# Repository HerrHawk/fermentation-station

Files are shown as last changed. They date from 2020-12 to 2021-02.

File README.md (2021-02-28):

# Fermenation Station

# About the Project

The motivation behind *Fermentation Station* was to have an easy way of maintaining a controlled environment (meaning temperature and humidity). Fermentation is a fickle process and maintaining the desired temperature and humidity in a stable manner is crucial for providing a safe and delicious product. Thus the premise is simple: have a contained system which handles everything you need to worry about. Set a target temperature and humidity value, put your produce in the box and come back in a couple of days to your ferment.

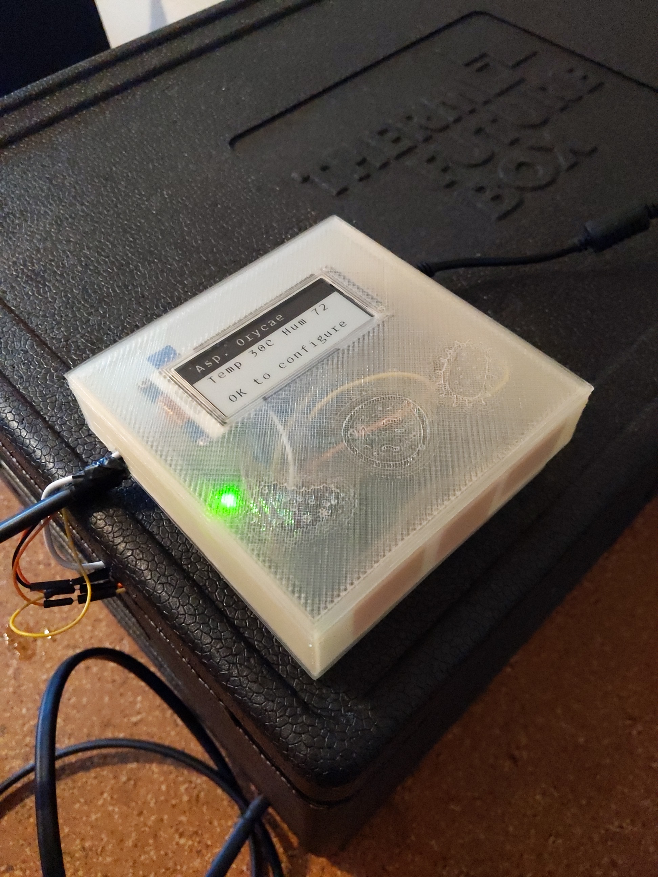
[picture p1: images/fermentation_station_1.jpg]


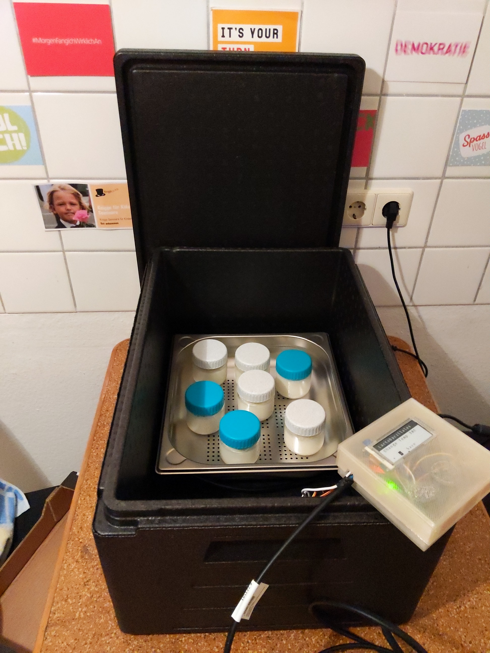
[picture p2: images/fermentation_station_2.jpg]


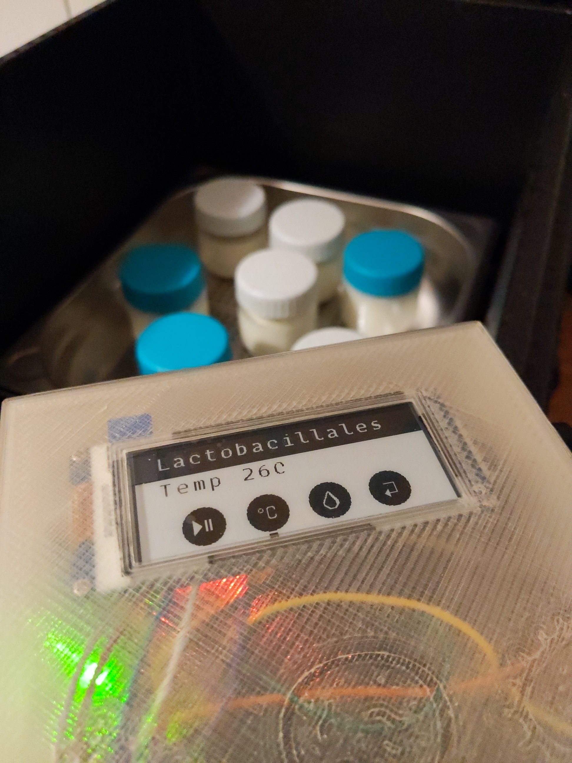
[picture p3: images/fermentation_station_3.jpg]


# How to use it

The user has three capacitive buttons to press: a `-`, `+` and `ok` button.

1. Connect the Fermentation Station to a power socket and wait for it to boot
2. On the recipe selection screen, use the `-` and `+` buttons to select a recipe
3. Confirm your selection with the `ok` button
4. If you need to, change the temperature and humidity to your desired values
5. Start the fermentation process
6. Come back in a couple of days and enjoy your ferment!

# Setup

## Hardware

|Product |Notes |Order |Datasheet |
|---|---|---|---|
|Adafruit Trinket Pro 3V |Main controller. Runs on 3.3V & comes with an onboard USB bootloader. |[Link](https://www.adafruit.com/product/2010) |[Link](https://cdn-shop.adafruit.com/datasheets/ATMEGA328P.pdf) |
|Arduino Uno |Used as a FTDI adapter for flashing and debugging the TrinketPro. |[Link](https://store.arduino.cc/arduino-uno-rev3) |[Link](http://ww1.microchip.com/downloads/en/DeviceDoc/Atmel-7810-Automotive-Microcontrollers-ATmega328P_Datasheet.pdf)|
|Bosch BME280 |Humidity/Temperature/Pressure Sensor (Pressure functionality is not used in this project). |[Link](https://www.reichelt.de/de/de/entwicklerboards-temperatur-feuchtigkeits-und-drucksensor--debo-bme280-p253982.html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) |[Link](https://www.mouser.de/datasheet/2/783/BST_BME280_DS002-1509607.pdf) |
|DEBO TOUCH SENS2 MPR121 |Capacitive touch controller with up to 12 Input channels (Three are used in this project). |[Link](https://www.reichelt.de/entwicklerboards-platine-fuer-kapazitive-beruehrungssensoren-mp-debo-touch-sens2-p291455.html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) |[Link](https://cdn-reichelt.de/documents/datenblatt/A300/DEBO_TOUCH_SENS2_DS_EN.pdf) |
|Waveshare 2.9inch e-Paper Module|E-Ink display for rendering information about the fermentation process. |[Link](https://www.reichelt.de/entwicklerboards-display-epaper-2-9-schwarz-weiss-debo-epa-2-9-p224224.html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) |[Link](https://www.waveshare.com/w/upload/9/98/2.9inch-e-paper-module-user-manual-en.pdf) |
|Ultrasonic Nebulizer |Compact humidifier, USB powered piezoelectric transducer that generates fine mist. |[Link](https://www.amazon.de/PEARL-Nebler-USB-Mini-Luftbefeuchter-Aroma-Diffuser/dp/B08591SF5G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) (Double Pack)|- |
|MOSFET Module DC 5V-36V 15A |Used to regulate the output of the heating element & humidifier. |[Link](https://www.amazon.de/gp/product/B07VRCXGFY/ref=ppx_yo_dt_b_asin_title_o03_s00?ie=UTF8&psc=1) (5 pcs) |- |
|DC/DC Step Down Buck Converter  |Converts the 24V from the Power Supply to 5V to drive the Arduino. A screwdriver and multimeter is required to set the correct output voltage.|[Link](https://www.amazon.de/gp/product/B08DNVXP87/ref=ppx_yo_dt_b_asin_title_o05_s00?ie=UTF8&psc=1) (6 pcs) |- |
|Thermo Box 42L |We used a 42 Liter Thermo Box for our prototype. In combination with the 30W Heatingcable we don't recommend going with a bigger box. |[Link](https://www.amazon.de/gp/product/B07B924LBB/ref=ppx_yo_dt_b_asin_title_o09_s00?ie=UTF8&psc=1) |- |
|Heating Cable 30W |24V 30W Heating cable with IPx7 protection. Ideal for our use-case. |[Link](https://www.amazon.de/gp/product/B00BAQW0OM/ref=ppx_yo_dt_b_asin_title_o01_s00?ie=UTF8&psc=1) |- |
|Power Supply 24 V 6A AC/DC | |[Link](https://www.amazon.de/gp/product/B0721MKCZJ/ref=ppx_yo_dt_b_asin_title_o03_s00?ie=UTF8&psc=1) |- |

Overall, the listed items set us back with around 140€. Costs could be reduced if we ordered from Chinese manufacturers via AliExpress, but this would result in much longer delivery times.

We choose all our components, if available, as breakout boards for an easy time while developing and prototyping. Since they aren't hardwired into the final prototype, they can easily be removed and reused for other projects.

Additionally, we used some miscellaneous hardware like breadboards, (jumper) wires and copper plates.

A soldering iron is also required for preparing the modules and building the prototype.

### Connecting the hardware

The schematic for this project is not too complicated. Since we choose manly hardware that is available as breakout boards and communicate via protocols like I²C and SPI, the wiring is kept at a minimum. While most of the build is only connecting pins, the chosen parts do need some preparation, before they can be used. Most of the components come with loose pin headers, which need to be soldered on to boards. After that, we are ready to go.  To get an idea of the whole build we created a breadboard and technical schematic in [fritzing](https://fritzing.org/). Some parts in the schematic defer from the ones in our part list, since they weren't available in fritzing, but the wiring stays the same. 

**Breadboard:**

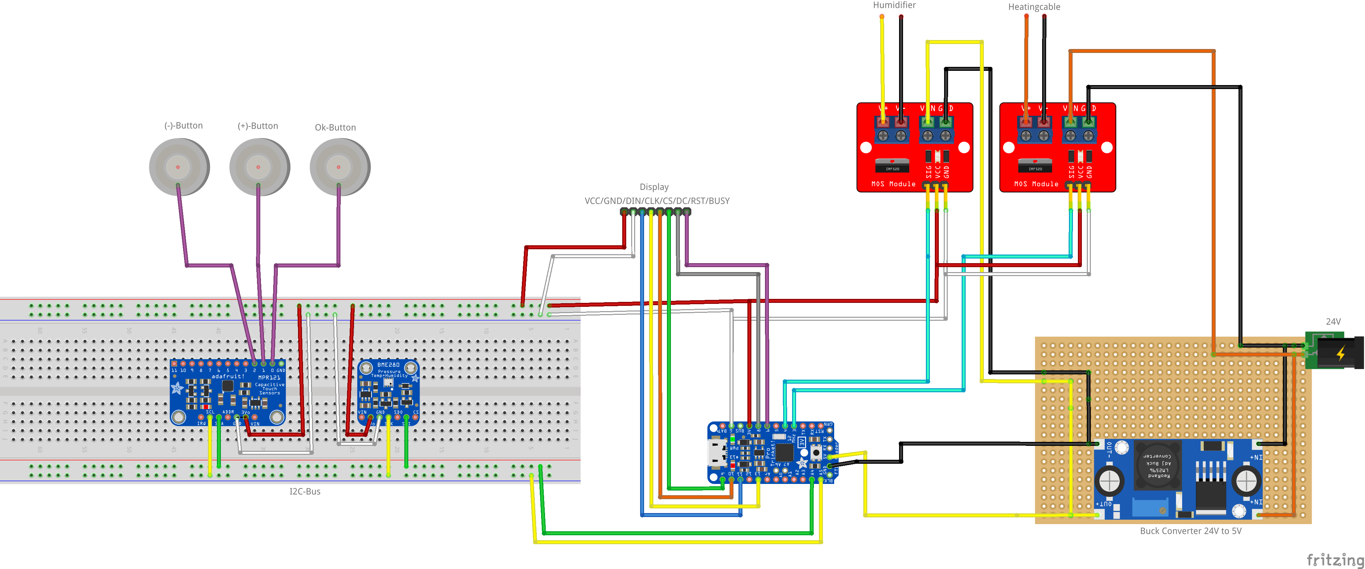
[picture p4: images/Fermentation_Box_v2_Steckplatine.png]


**Circuit diagram:**

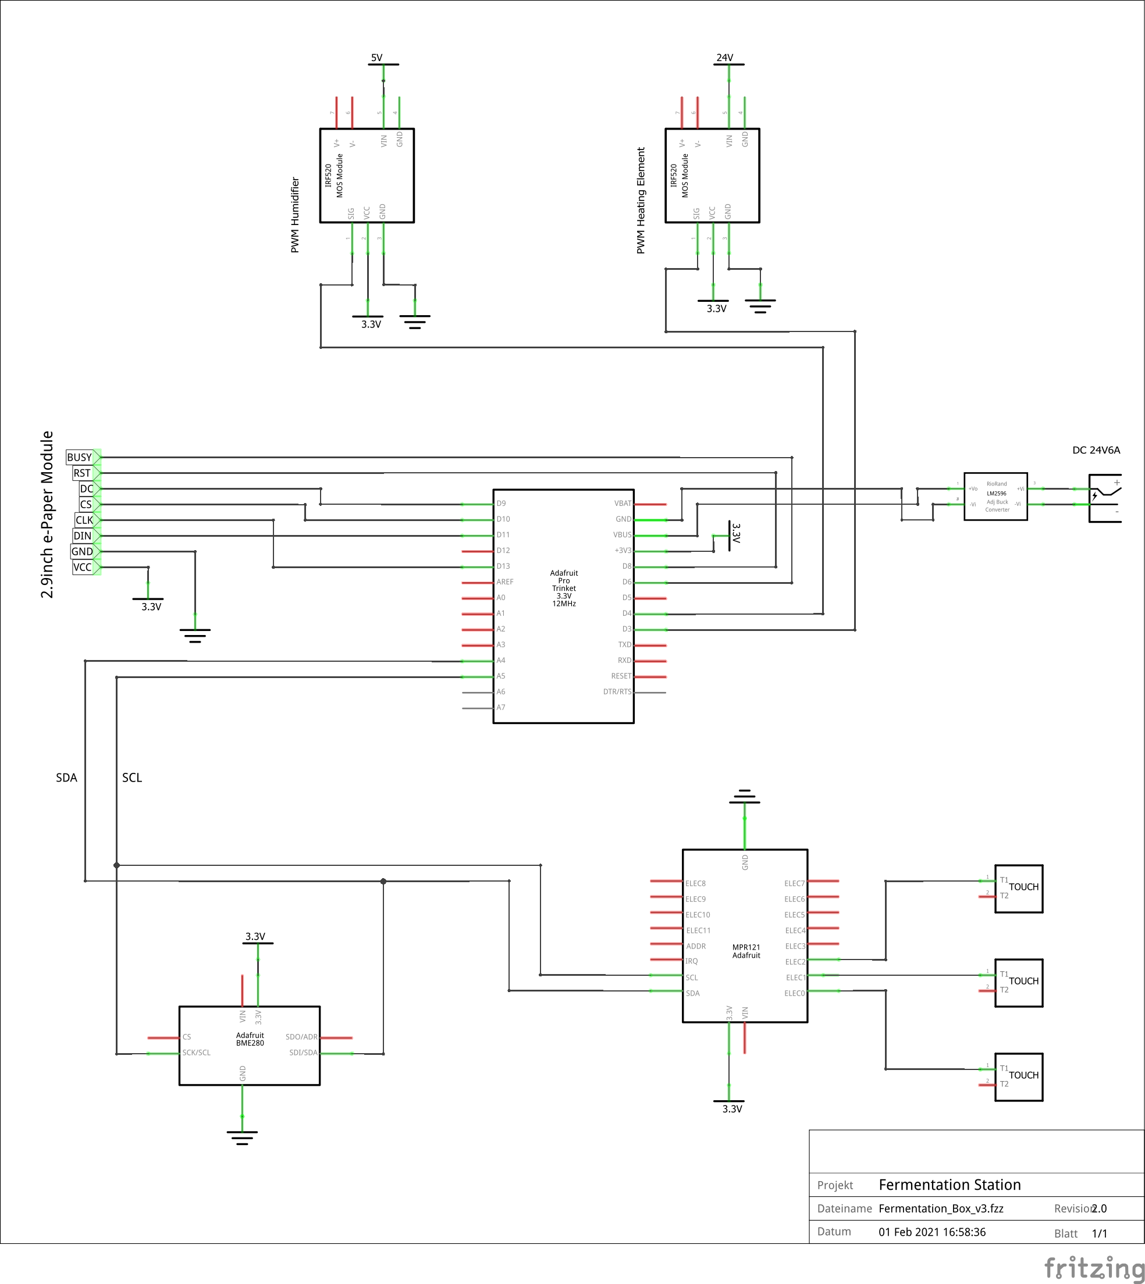
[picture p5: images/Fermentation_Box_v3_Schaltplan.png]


### Testing the individual components

Before putting everything together we recommend testing the individual parts separately. During our build we encountered problems especially with the e-Ink display. Checking the bought hardware early will prevent unnecessary delays later on. 

The chosen components come all with example code from the manufacturers or distributors like Adafruit. All the examples can be built and run with the Arduino IDE.

- **Waveshare e-Ink Display: [GitHub](https://github.com/waveshare/e-Paper)**
    - Run the demo code in */Arduino/epd2in9/epd2in9.ino*
    - If the TrinketPro is used for testing, change the BUSY pin defined in /Arduino/epd2in9/epdif.h from 7 to 6. (Pin 7 on the TrinketPro isn't exposed and reserved for the onboard USB connection)
- **BME280: [Adafruit](https://learn.adafruit.com/adafruit-bme280-humidity-barometric-pressure-temperature-sensor-breakout/arduino-test)**
    - On the linked website you find a detailed explanation on how to add and run the example code in the Arduino IDE for the BME280-Sensor.
- **MPR121: [Adafruit](https://learn.adafruit.com/adafruit-mpr121-12-key-capacitive-touch-sensor-breakout-tutorial?view=all)**
    - Same goes for the touch sensor. Add the example code to the IDE and test the touch sensor.
    - After testing the touch sensor we recommend switching to bigger electrodes. This makes controlling and testing the fermentation station easier. We used simple [copper foil](https://www.conrad.de/de/p/pb-fastener-kupferfolie-selbstklebend-l-x-b-150-mm-x-30-mm-inhalt-10-st-529532.html) to build our electrodes.

After testing the individual components they can be combined according to our schematics.

After development, we tried to go for a more permanent setup. We replaced the breadboard with a perfboard. Instead of soldering our microcontroller and sensors directly onto the perfboard we used pin headers, so the modules can be easily attached or removed if we want to reuse them for other projects. Since it was our first attempt at soldering a permanent prototype the result isn't perfect, but it does the job.

To prevent damage to the hardware components and wiring we 3D-printed a simple case for our prototype. We added a cutout in the top of the box for the display. The electrodes were placed inside the box. The electrodes can reliably detect touch input through the plastic - No buttons needed!

<!-- ![images/fermentation_station_4.jpg](images/fermentation_station_4.jpg) -->
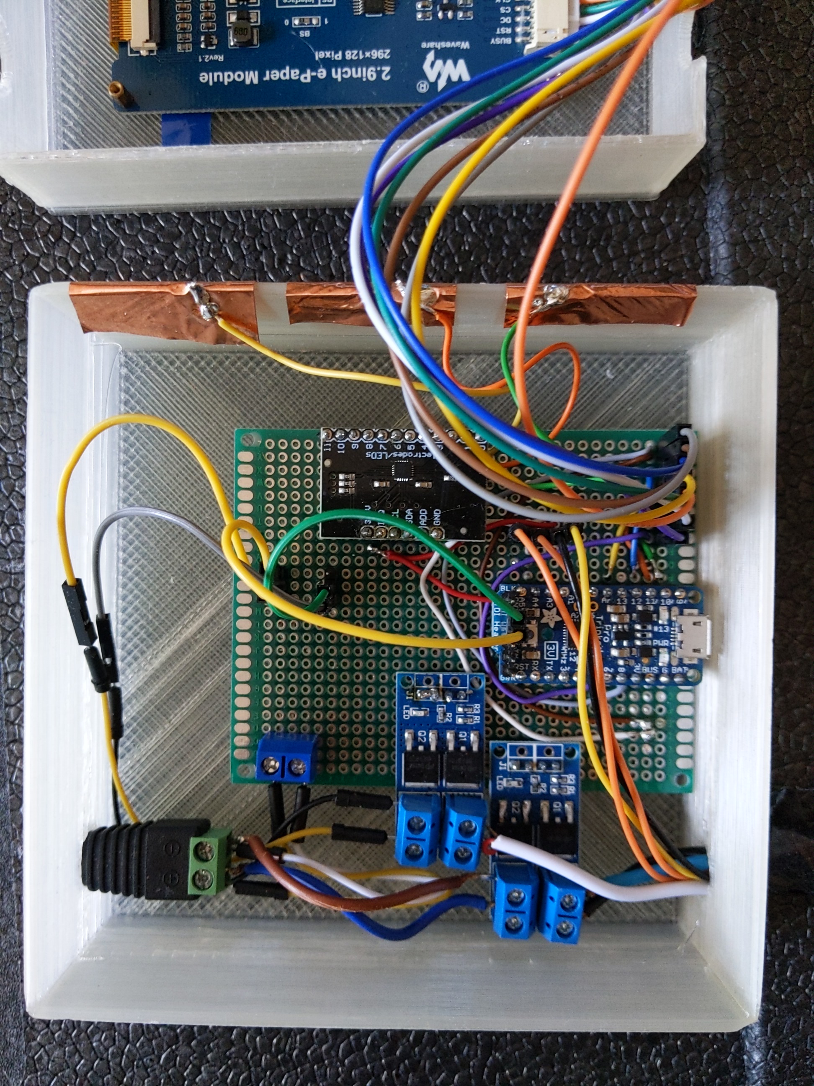
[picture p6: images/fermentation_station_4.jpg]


<!-- ![images/fermentation_station_5.jpg](images/fermentation_station_5.jpg) -->
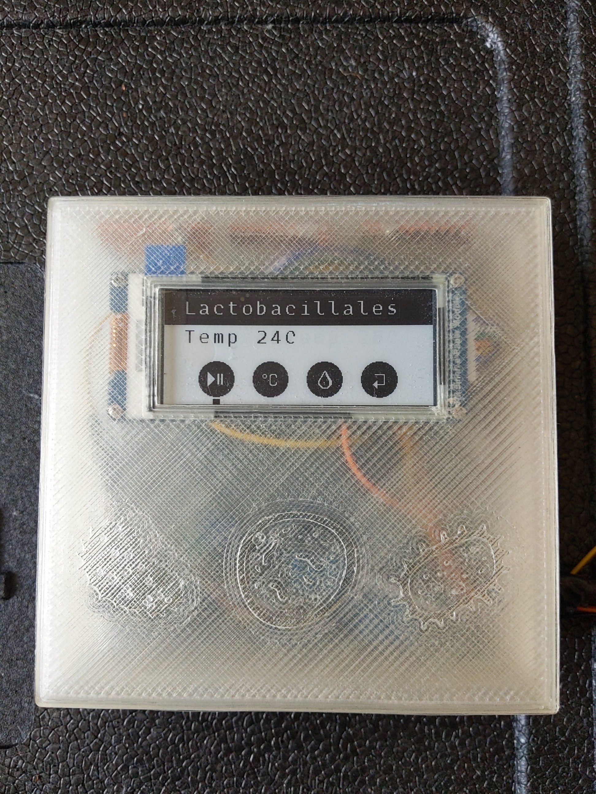
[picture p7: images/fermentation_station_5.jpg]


## Software

The project is written in embedded C, no external libraries are used. Additionally, for font rendering we use Python to create the individual character bitmaps.

### Building and Flashing

To be able to build and flash the firmware onto the microcontroller, you need to have [avr-gcc](https://www.google.com/search?client=safari&rls=en&q=avrgcc&ie=UTF-8&oe=UTF-8) and avrdude installed. On Windows, [WinAVR](http://winavr.sourceforge.net) can be used as an alternative to avr-gcc. 

The build process is handled via a Makefile. In order to get started with building, simply execute the following commands in the root folder of the repository.

```bash
> cd <repo-dir>
> mkdir build
> make clean
> make build
> make flash
```

`make clean` sets us up with a bland slate, deleting all files created in the build process. This also forces a complete rebuild.

`make build` bundles all the code into a format that can be flashed onto the microcontroller.

`make flash` flashes the previously build .hex file onto the microcontroller. This also executes `build` beforehand.

## Implementation Details

### Design Principles

- Rely on CI/CD for catching breaking changes early
- Clang format for enforced coding styles
- As functional as possible - no faked Classes in C!
- Work with git and feature branches

### Architecture

Our architecture consists of a hardware interface layer, a driver layer, a controller layer and the main program flow which is implemented as a state machine. We have split the code in modules beginning from the components that communicate directly with the hardware up to the high-level functions that we use to control the sensors & actors. This keeps the code well-arranged. 

- The Hardware Interfaces Layer represents the low-level protocols that we implemented. In our project SPI is used to communicate with the display, UART for writing to the display and I2C for retrieving sensor information from the temperature/humdity sensor and the touch sensor.
- The Drivers Layer contains an API that our controller layer can use to execute functions that work on the different hardware components.
- The Controller Layer provides high-level functions to interact with the different hardware and sensors. An example is the Renderer that can write text and images onto the display. Some example functions and more implementation details on the Renderer are shown in chapter Font and Image Rendering
- The state machine, which is explained in detail in the following chapter, is used to control the program flow. Additionally, it writes errors that occur to the Serial Port (using our Logging controller).

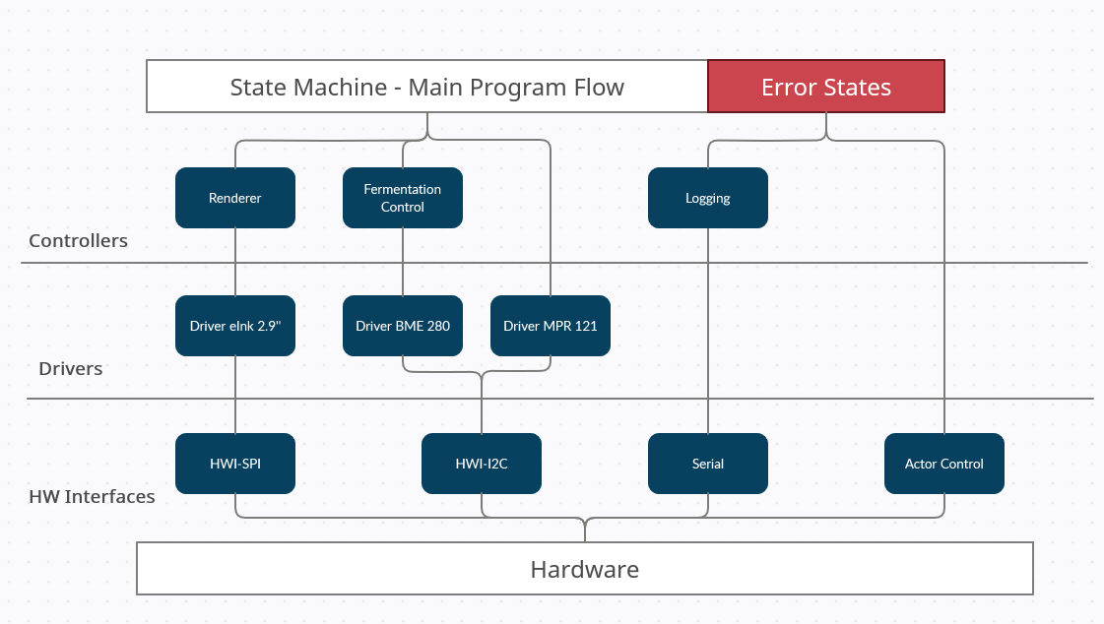
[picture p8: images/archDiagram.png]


### State Machine

For controlling the main program flow we used a state machine. The state machine helps us to permanently query the touch sensor for user input. If the touch sensor receives any input it writes to an input register which in turn gets requested by the main program flow. If a state change occurs the state machine triggers the Font and Image Rendering process to update the display.

The following graphic visualizes the main program flow handled by our state machine. On start, the program displays the Recipe Selection menu. Once the user has selected a recipe the state machine switches to the Fermentation Process. The user can then access the sub-menus for Temperature Change or Humidity Change or may end the Fermentation Process and return to the Recipe Selection.

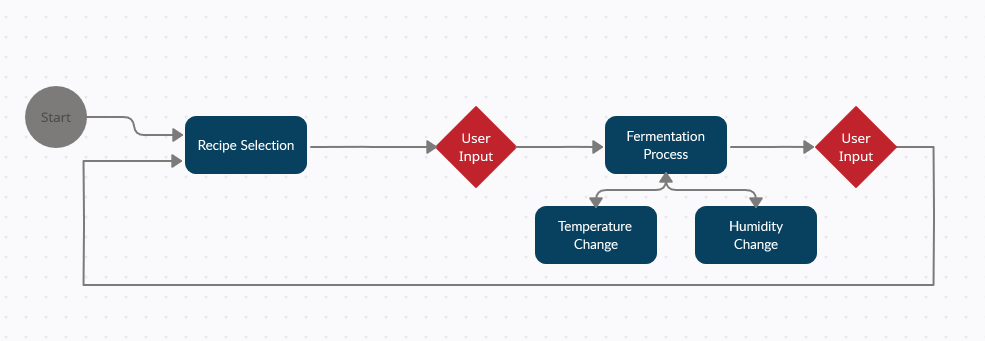
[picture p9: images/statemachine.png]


### PID Controller

To keep our temperature steady we decided to implement a PID controller. A PID (proportional-integral-derivative) controller is a control loop that uses error calculations and three basic mathematic formulas to achieve a constant convergence towards our desired temperature or humidity value.

The values to control how the controller operates are called *control terms* and have to be determined by experimentation. To achieve this, we conducted several test fermentations to determine the *control terms* and optimized them towards values that work for our use-case.

With this implementation we now have a mechanism that controls the power supply for our heat cable and nebulizer so that heat and humidity reach the desired values and maintain them at a steady level.

The following graphic is a plot of the actual temperature and our desired temperature in an example fermentation process. In this example the controller regulates the temperature to around 1°C around the desired value of 29°C.

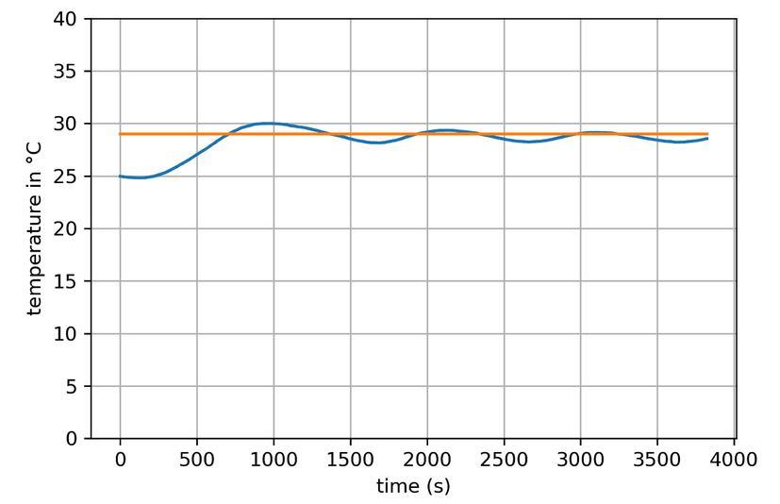
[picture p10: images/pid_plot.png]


### Font and Image Rendering

We use a Waveshare 2.9" black and white e-Ink Display as our main method of providing feedback to the user. This is done by showing information like the currently selected recipe, as well as the current temperature and humidity.

Images and text are written to the display as bitmaps, which ,due to the type of controller used on the display, needs to adhere to multiples of 8, as it doesn't support bitwise updates of the frame memory.

Both images and text were prepared with python. The font was rendered out using the Pillow Image library and exported as a series of hex arrays. The images received the same treatment. All steps required for turning a font into a usable bitmap can be seen in the provided jupyter notebook, `font_rendering.ipynb`.



An example of what the rendered font looks like

The process of getting elements to render on the display is fairly complex and very specific to this controller. Also, the display is intended to be used narrow side up, so the indexing of the display memory didn't translate well to our intended use of placing the display wide side up. In order to have an easier interaction with the display, we implemented an additional layer of utility functions on top of the underlying rendering methods. Thus, after the renderer was completed we only needed to use the following functions:

```c
void print_text(const char* string, int x, int y, int white_on_black);
void show_image(const unsigned char* image_buffer, int x, int y, int width, int height, int invert);
void draw_box(int color, int x, int y, int width, int height);
void display_wipe(void);
void display_render_frame(void);
```

One of the main things to keep in mind about the display is that it manages two different frame memory areas. This is due to historic reasons and isn't really justified today whatsoever - but it kept the price for the eInk display low. Basically, the display alternates between these two areas when deciding what to actually put on the display. This requires for different approaches when updating the display depending on the purpose of the update.

**Purpose 1**: Updating a fixed element on the screen. In order to have all elements not flicker around, they need to be written and rendered twice.

**Purpose 2**: In case of elements that are updated every step, it's enough to write it once. This saves a bit of time because we don't have to render everything twice.

# Outlook

We couldn't test yet how the software behaves if it runs for an extended period (some fermentation recipes have to run for 6 months). So this is definitely something that has to be tested. 

Also, we are not entirely happy with the performance of the Renderer. Sometimes the rendering process takes a bit longer than we would like it to. So we want to make some performance optimisations to the Renderer and the State Machine.

As the cherry on top we would like to design our own PCB with all the necessary components on it, as well as some fancy capacitive touch buttons etched into its surface. While we have all the functionality we want integrated into our fermentation station, the presentation is still a bit lacking - but nothing that a bit of eye candy cannot fix.

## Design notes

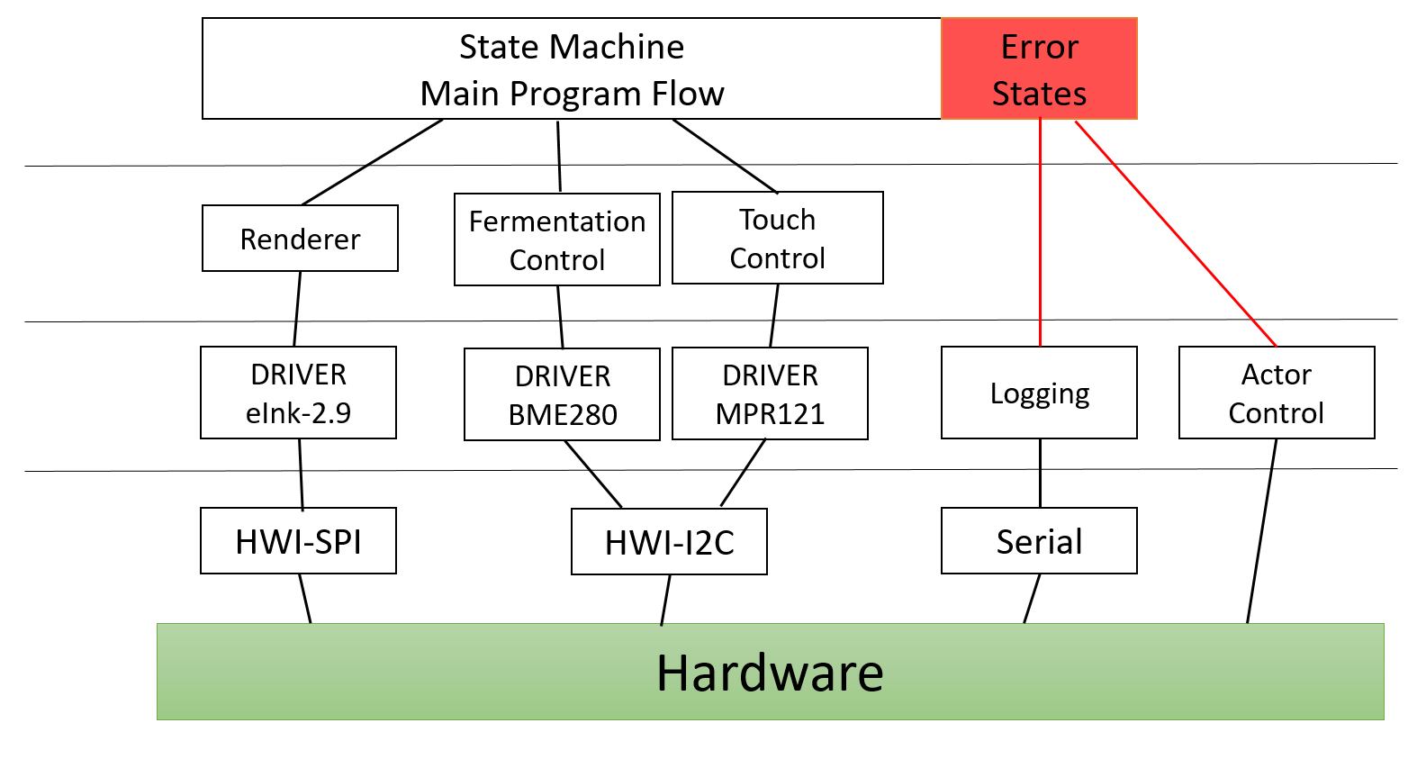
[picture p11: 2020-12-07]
presentations/archDiagramVersion0.1.PNG

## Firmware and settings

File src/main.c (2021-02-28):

#include "controller/fermentation.h"
#include "controller/renderer.h"
#include "drivers/bme280.h"
#include "drivers/mpr121.h"
#include "globals.h"
#include "helpers.h"
#include "interfaces/i2c.h"
#include "logging.h"
#include "timer.h"
#include <avr/io.h>
#include <util/delay.h>

// Types needed for state machine program architecture
struct state;
typedef void state_fn(struct state*);
struct state
{
  state_fn* next;
  int pass_data;
};

// Our pre-defined recipes to be selected for a fermentation process
/*
// Lactofermentierung, 25° (28° optimal), no humidity (-1 means perma off)
// Symbiotic Culture of Bacteria and Yeast, 25° (28° optimal), no hum (-1 means perma off)
// Koji, 30°, 72% humidity
*/
struct recipe recipes[] = { { "Lactobacillales", 2500, -1, 0 },
                            { "SCOBY", 2500, -1, 0 },
                            { "Asp. Orycae", 3000, 72000, 7000 },
                            { "Test1", 4500, -1, 0 },
                            { "Test2", 5000, 60000, 6000 } };

// Global variable that determines which one of the recipes is currently selected
int8_t recipe_counter;
// Global variable that determines which of the context menu buttons in the
// fermentation menu is selected
int8_t change_context;
// Global variable that determines which of the context menu buttons in the temp /
// hum sub-menus is selected
int8_t submenu_change_context;
// Global variable that tells the program whether a fermentation is currently running or not
uint8_t fermentation_started;

// Declaring functions as states for the state machine
state_fn recipe_selection;
state_fn fermentation_process;

// Setting the recipe counter in a cyclic type of list that returns
// to the beginning/end when reaching the max or min value
void set_recipe_counter(int8_t modifier)
{
  recipe_counter = recipe_counter + modifier;
  // Get the size of the array
  int8_t size = (sizeof(recipes) / sizeof(recipes[0]));

  if (recipe_counter == -1) {
    // If the recipe counter is at -1 -> set counter to last element in array
    recipe_counter = size - 1;
  } else if (recipe_counter == size) {
    // If the recipe counter exceeds the maximum range return to the first element
    recipe_counter = 0;
  }

  LOG_DEBUG(DEFAULT, "recipe counter is now %d", recipe_counter);
}

// Setting the fermentation menu change context in a cyclic type of list that returns
// to the beginning/end when reaching the max or min value
void set_change_context(int8_t modifier)
{
  // Change context :
  // 0: idle
  // 1: change temperature
  // 2: change humidity
  // 3: exit
  change_context = change_context + modifier;

  if (change_context == -1) {
    change_context = 3;
  } else if (change_context == 4) {
    change_context = 0;
  }

  LOG_DEBUG(DEFAULT, "change_context is now %d", change_context);
}

// Setting the temp/hum sub-menu change context in a cyclic type of list that returns
// to the beginning/end when reaching the max or min value
void set_submenu_change_context(int8_t modifier)
{
  // Submenu Change context :
  // 0: plus
  // 1: minus
  // 2: Exit
  submenu_change_context = submenu_change_context + modifier;

  if (submenu_change_context == -1) {
    submenu_change_context = 2;
  } else if (submenu_change_context == 3) {
    submenu_change_context = 0;
  }

  LOG_DEBUG(DEFAULT, "submenu change_context is now %d", submenu_change_context);
}

// The main menu waits for user touch input then starts fermentation with a predefined recipe
void recipe_selection(struct state* state)
{
  LOG_DEBUG(CONTROL, "entering recipe selection menu");

  // initialize the main menu with the first recipe (recipes[0]) -> reset counter
  recipe_counter = 0;
  // Rendering the first recipe onto the display
  render_recipe(recipes[recipe_counter].recipe_name,
                recipes[recipe_counter].desired_temp,
                recipes[recipe_counter].desired_hum);

  for (;;) {

    LOG_DEBUG(CONTROL, "wait for user touch input");
    // Read the touch input on the register in which the touch sensor writes
    // 0b001 : Button 1
    // 0b010 : Button 2
    // 0b100 : Button 3
    uint8_t touch_input = get_touch();

    _delay_ms(10);

    switch (touch_input) {
      case 0b001: // (+) button pressed
        // Increment the recipe counter
        set_recipe_counter(1);
        // Re-render the display with the the next recipe
        render_recipe(recipes[recipe_counter].recipe_name,
                      recipes[recipe_counter].desired_temp,
                      recipes[recipe_counter].desired_hum);
        break;

      case 0b010: // (-) button pressed
        // Decrement the recipe counter
        set_recipe_counter(-1);
        // Re-render the display with the previous recipe
        render_recipe(recipes[recipe_counter].recipe_name,
                      recipes[recipe_counter].desired_temp,
                      recipes[recipe_counter].desired_hum);
        break;

      case 0b100: // (ok) button pressed
        LOG_DEBUG(DEFAULT, "switching state to fermentation");

        // Switch the state machine over to fermentation process
        state->next = fermentation_process;
        return;

      default:
        // No touch input received -> Do nothing, next iteration of loop
        break;
    }
  }
}

// The fermentation process regulates temp and hum and also waits for user input to start/cancel the
// ferment or alter temp or hum in a sub-menu
void fermentation_process(struct state* state)
{
  // Renders the fermentation menu overview

  if (!fermentation_started) {
    render_ferm_start(recipes[recipe_counter].recipe_name, change_context);
  }
  // Get current temp and hum
  int32_t c_temp = bme280_read_temp();
  uint32_t c_hum = recipes[recipe_counter].desired_hum != -1 ? bme280_read_hum() : -1;

  // Render recipe overview including the submenu buttons
  // Display current temp and hum
  render_recipe_and_submenus(
    recipes[recipe_counter].recipe_name, c_temp, c_hum, change_context, fermentation_started);
  LOG_DEBUG(
    CONTROL, "starting fermentation process with recipe %s ", recipes[recipe_counter].recipe_name);

  // Remember the change context (which button is highlighted/selected)
  int8_t last_context = change_context;

  for (;;) {
    // loop until a touch input has been detected
    // if nothing happens, this will just idle here and continuosly update
    // temperature and humidity
    uint8_t touch_input = get_touch();
    while (!touch_input) {
      LOG_DEBUG(DEFAULT, "no touch input received");

      // If the fermentation process is running, check the temp and hum and let the pid controller
      // control the heating and humidity control process
      if (fermentation_started && s1_triggered) {
        // Check temperature and humidity
        // if the humidity isn't part of the recipe, the returned -1 will disable
        // printing for the humidity part of the interface
        c_temp = check_temp(&recipes[recipe_counter]);
        c_hum = check_hum(&recipes[recipe_counter]);
        render_temperature_and_humidity(c_temp, c_hum);
      }
      // check whether touch input has been received by now
      touch_input = get_touch();
    }

    _delay_ms(10);

    // Interpret the touch input
    // 0b001 : Button 1
    // 0b010 : Button 2
    // 0b100 : Button 3
    switch (touch_input) {
      case 0b001: // (+) button
        // Increment the change context and get back to requesting user input
        set_change_context(1);
        return;
        break;
      case 0b010: // (-) button
        // Decrement the change context and get back to requesting user input
        set_change_context(-1);
        return;
        break;
      case 0b100: // (ok) button
        break;
      default:
        break;
    }

    // char* test[3];
    // sprintf(test, "%d", change_context);
    // print_text(test, 0, 0, 0);
    // display_render_frame();
    // _delay_ms(1500);

    // Change context :
    // 0: idle                  --> switch fermentation on or off
    // 1: change temperature    --> switch to submenu to change temp of the recipe
    // 2: change humidity       --> switch to submenu to change hum of the recipe
    // 3: exit                  --> exit and go back to recipe selection menu

    switch (change_context) {
      case 0: // (idle context btn) -> start/stop fermentation
        // Fermentation start/stop
        if (fermentation_started == 0) {
          LOG_DEBUG(CONTROL, "fermentation has been started");
          fermentation_started = 1;
        } else {
          LOG_DEBUG(CONTROL, "fermentation has been stopped");
          fermentation_started = 0;
          change_context = 0;
          // Render the fermentation starting menu and its buttons
          render_ferm_start(recipes[recipe_counter].recipe_name, change_context);
          render_recipe_and_submenus(recipes[recipe_counter].recipe_name,
                                     recipes[recipe_counter].desired_temp,
                                     recipes[recipe_counter].desired_hum,
                                     change_context,
                                     fermentation_started);
        }
        return;
        break;
      case 1: // change temp context
        // Switch to sub-menu for temperature change
        sub_menu_temperature_change();
        // After changing the temp, re-render the display with the new required temperature
        render_recipe_and_submenus(recipes[recipe_counter].recipe_name,
                                   recipes[recipe_counter].desired_temp,
                                   recipes[recipe_counter].desired_hum,
                                   change_context,
                                   fermentation_started);
        LOG_DEBUG(DEFAULT, "implement me: temp change");
        return;
        break;
      case 2: // change hum context
        LOG_DEBUG(DEFAULT, "implement me: hum change");

        if (recipes[recipe_counter].desired_hum != -1) {
          // Switch to sub-menu for humidity change
          sub_menu_humidity_change();
          // After changing the hum, re-render the display with the new required humidity
          render_recipe_and_submenus(recipes[recipe_counter].recipe_name,
                                     recipes[recipe_counter].desired_temp,
                                     recipes[recipe_counter].desired_hum,
                                     change_context,
                                     fermentation_started);
        }
        break;
      case 3: //(exit context btn)

        // Return to recipe selection
        state->next = recipe_selection;
        return;
      default: // This should never happen, because cases are predefined from 0-3
        LOG_DEBUG(DEFAULT, "FATAL ERROR");
        break;
    }
  }
}

// nested loop method in fermentation_process
// "invisible nested state"
void sub_menu_temperature_change()
{
  submenu_change_context = 0;
  // Render the submenu-view for temperature change
  // with the recipe's base data for temperature
  render_submenu_temp(recipes[recipe_counter].recipe_name,
                      recipes[recipe_counter].desired_temp,
                      submenu_change_context);

  for (;;) {
    // Read the touch input on the touch sensor
    // 0b001 : Button 1
    // 0b010 : Button 2
    // 0b100 : Button 3
    uint8_t touch_input = get_touch();

    _delay_ms(10);

    switch (touch_input) {
      case 0b001: // (+) button
        // Increment sub menu selection context
        set_submenu_change_context(1);
        // Re-render the submenu with the new selected btn
        render_submenu_temp(recipes[recipe_counter].recipe_name,
                            recipes[recipe_counter].desired_temp,
                            submenu_change_context);
        break;
      case 0b010: // (-) button
        // Decrement sub menu selection context
        set_submenu_change_context(-1);
        // Re-render the submenu with the new selected btn
        render_submenu_temp(recipes[recipe_counter].recipe_name,
                            recipes[recipe_counter].desired_temp,
                            submenu_change_context);
        break;
      case 0b100: // (OK) button

        // Submenu Change context :
        // 0: plus      --> Increment temperature
        // 1: minus     --> Decrement temperature
        // 2: Exit      --> Exit (and save but that happens implicitly)
        switch (submenu_change_context) {
          case 0: // Increment temp
            // update temp value in recipe + 1 °C
            recipes[recipe_counter].desired_temp += 100;
            // Re-render with new temp
            render_submenu_temp(recipes[recipe_counter].recipe_name,
                                recipes[recipe_counter].desired_temp,
                                submenu_change_context);
            break;
          case 1: // Decrement temp
            // update temp value in recipe - 1 °C
            recipes[recipe_counter].desired_temp -= 100;
            // Re-render with new temp
            render_submenu_temp(recipes[recipe_counter].recipe_name,
                                recipes[recipe_counter].desired_temp,
                                submenu_change_context);
            break;
          case 2: // Exit submenu
            return;

          default:
            break;
        }
        break;
      default:
        break;
    }
  }
}

// nested loop method in fermentation_process
// "invisible nested state"
void sub_menu_humidity_change()
{
  submenu_change_context = 0;
  // Render the submenu-view for humdity change
  // with the recipe's base data for humidity
  render_submenu_hum(recipes[recipe_counter].recipe_name,
                     recipes[recipe_counter].desired_hum,
                     submenu_change_context);

  for (;;) {
    // Read the touch input on the touch sensor
    // 0b001 : Button 1
    // 0b010 : Button 2
    // 0b100 : Button 3
    uint8_t touch_input = get_touch();

    _delay_ms(10);

    switch (touch_input) {
      case 0b001: // (+) button
        // Increment sub menu selection context
        set_submenu_change_context(1);
        // Re-render the submenu with the new selected btn
        render_submenu_hum(recipes[recipe_counter].recipe_name,
                           recipes[recipe_counter].desired_hum,
                           submenu_change_context);
        break;
      case 0b010: // (-) button
        // Decrement sub menu selection context
        set_submenu_change_context(-1);
        // Re-render the submenu with the new selected btn
        render_submenu_hum(recipes[recipe_counter].recipe_name,
                           recipes[recipe_counter].desired_hum,
                           submenu_change_context);
        break;
      case 0b100: // (OK) button

        // Submenu Change context :
        // 0: plus      --> Increment temperature
        // 1: minus     --> Decrement temperature
        // 2: Exit      --> Exit (and save but that happens implicitly)
        switch (submenu_change_context) {
          case 0: // Increment hum
            // update hum value in recipe + 1 %
            recipes[recipe_counter].desired_hum += 1000;
            // Re-render with new hum
            render_submenu_hum(recipes[recipe_counter].recipe_name,
                               recipes[recipe_counter].desired_hum,
                               submenu_change_context);
            break;
          case 1: // Decrement hum
            // update temp value in recipe - 1 %
            recipes[recipe_counter].desired_hum -= 1000;
            // Re-render with new hum
            render_submenu_hum(recipes[recipe_counter].recipe_name,
                               recipes[recipe_counter].desired_hum,
                               submenu_change_context);
            break;
          case 2: // Exit submenu
            return;

          default:
            break;
        }
        break;
      default:
        break;
    }
  }
}

// Dummy method for occurring errors
void error_function()
{
  LOG_DEBUG(DEFAULT, "error occurred, writing to log");
  _delay_ms(2500);
}

void fermentation_init(void)
{
  change_context = 0;
  fermentation_started = 0;
}

int main(void)
{
  // run setup/initialization functions
  uart_init();
  i2c_init();
  _delay_ms(10);
  mpr121_init();
  bme280_init();
  setup_heating_element();
  setup_timer_s1();

  display_init();

  // Initialize state machine with initial state "wait for touch"
  // (waiting for user input after init)
  struct state state = { recipe_selection, 0 };
  display_wipe();

  while (1) {
    state.next(&state);
  }
  return 0;
}

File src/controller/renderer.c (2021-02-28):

#include "renderer.h"
#include "../globals.h"
#include "../graphics/font.h"
#include "../graphics/images.h"
#include "../interfaces/spi.h"
#include "../logging.h"
#include <avr/pgmspace.h>
#include <stdio.h>
#include <stdlib.h>
#include <util/delay.h>

/**
 * The information for this part of the program was taken mainly from three sources:
 *  - datasheet of the display
 * https://www.waveshare.com/w/upload/9/98/2.9inch-e-paper-module-user-manual-en.pdf
 *  - datasheet of the display controller
 * https://www.smart-prototyping.com/image/data/9_Modules/EinkDisplay/GDE029A1/IL3820.pdf
 *  - the official code examples by waveshare: https://github.com/waveshare/e-Paper
 */

// PORTS on the display
#define RST_PIN PB0
#define DC_PIN PB1
#define CS_PIN PB2
#define BUSY_PIN PD6

#define BAUD 9600

// define display commands p. 12 - 16
#define DRIVER_OUTPUT_CONTROL 0x01
#define BOOSTER_SOFT_START_CONTROL 0x0C
#define GATE_SCAN_START_POSITION 0x0F
#define DEEP_SLEEP_MODE 0x10
#define DATA_ENTRY_MODE_SETTING 0x11
#define SW_RESET 0x12
#define TEMPERATURE_SENSOR_CONTROL 0x1A
#define MASTER_ACTIVATION 0x20
#define DISPLAY_UPDATE_CONTROL_1 0x21
#define DISPLAY_UPDATE_CONTROL_2 0x22
#define WRITE_RAM 0x24
#define WRITE_VCOM_REGISTER 0x2C
#define WRITE_LUT_REGISTER 0x32
#define SET_DUMMY_LINE_PERIOD 0x3A
#define SET_GATE_TIME 0x3B
#define BORDER_WAVEFORM_CONTROL 0x3C
#define SET_RAM_X_ADDRESS_START_END_POSITION 0x44
#define SET_RAM_Y_ADDRESS_START_END_POSITION 0x45
#define SET_RAM_X_ADDRESS_COUNTER 0x4E
#define SET_RAM_Y_ADDRESS_COUNTER 0x4F
#define TERMINATE_FRAME_READ_WRITE 0xFF

// lookuptables to be used by the display for correctly accessing and modifying its memory
const unsigned char lut_full_update[] = { 0x50, 0xAA, 0x55, 0xAA, 0x11, 0x00, 0x00, 0x00,
                                          0x00, 0x00, 0x00, 0x00, 0x00, 0x00, 0x00, 0x00,
                                          0x00, 0x00, 0x00, 0x00, 0xFF, 0xFF, 0x1F, 0x00,
                                          0x00, 0x00, 0x00, 0x00, 0x00, 0x00 };

const unsigned char lut_partial_update[] = { 0x10, 0x18, 0x18, 0x08, 0x18, 0x18, 0x08, 0x00,
                                             0x00, 0x00, 0x00, 0x00, 0x00, 0x00, 0x00, 0x00,
                                             0x00, 0x00, 0x00, 0x00, 0x13, 0x14, 0x44, 0x12,
                                             0x00, 0x00, 0x00, 0x00, 0x00, 0x00 };

/**
 * Wait until the display has finished processing
 */
inline void display_wait_until_idle(void)
{
  while (PORTD & _BV(BUSY_PIN)) {
    _delay_ms(100);
  };
}

/**
 * Send a command to the display
 *
 * @param command the command to send
 */
void display_send_command(uint8_t command)
{
  // may not send commands while display is busy
  display_wait_until_idle();

  // make display interpret data as command
  // by setting the Data/Command pin to low
  // high pin would lead to interpretation as data
  PORTB &= ~_BV(DC_PIN);

  // send command
  spi_main_transmit(command);
}

/**
 * Send a piece of data to the display
 *
 * @param data the data to send
 */
void display_send_data(uint8_t data)
{
  // may not send data while display is busy
  display_wait_until_idle();

  // make display interpret data as command
  // by setting the Data/Command pin to low
  // low pin would lead to interpretation as command
  PORTB |= _BV(DC_PIN);

  // send data
  spi_main_transmit(data);
}

/**
 * Reset the display. This is basically a soft reboot
 */
void display_reset(void)
{
  // the display may be reset by simply toggling the Reset Pin
  PORTB &= ~_BV(RST_PIN);
  // leave some time for the display to actually reset
  _delay_ms(200);
  PORTB |= _BV(RST_PIN);
  _delay_ms(200);
}

/**
 * Set the lookup table of the display. Different LUTs need to
 * be used when updating the entire display memory or only parts of it.
 *
 * @param lut the lookup table to be set on the display.
 *
 * @see lut_full_update
 * @see lut_partial_update
 */
void display_set_lookup_table(const unsigned char* lut)
{
  // different lookup tables are used when we update either
  // the entire display or only parts of it
  display_send_command(WRITE_LUT_REGISTER);
  // look up table is 30 bytes long
  for (int i = 0; i < 30; i++) {
    display_send_data(lut[i]);
  }
}

/**
 * Update only a part of the displays frame memory.
 *
 * @param image_buffer the bytearray to write to the display
 * @param x the x coordinate of the most upper left pixel
 * @param y the y coordinate of the most upper left pixel
 * @param image_width the width of the image
 * @param image_height the height of the image
 * @param stored_on_flash whether the image_buffer needs to be accessed from flash
 * @param overwrite an optional value to overwrite the values of the image buffer with
 * @param invert bitwise invert the image
 */
void display_set_partial_frame_memory(const unsigned char* image_buffer,
                                      int x,
                                      int y,
                                      int image_width,
                                      int image_height,
                                      int stored_on_flash,
                                      int overwrite,
                                      int invert)
{
  // only continue if action is valid
  if (image_buffer == NULL || x < 0 || y < 0 || image_width < 1 || image_height < 1) {
    return;
  }

  // to set only a part of the frame memory, the display needs to use the partial frame mempory
  display_set_lookup_table(lut_partial_update);

  // x must be the multiple of 8 or the last 3 bits will be ignored
  x &= 0xF8;
  image_width &= 0xF8;

  // determine the end index of the image
  int x_end;
  int y_end;
  if (x + image_width >= DISPLAY_WIDTH) {
    x_end = DISPLAY_WIDTH - 1;
  } else {
    x_end = x + image_width - 1;
  }
  if (y + image_height >= DISPLAY_HEIGHT) {
    y_end = DISPLAY_HEIGHT - 1;
  } else {
    y_end = y + image_height - 1;
  }

  // prepare send to display
  display_set_memory_area(x, y, x_end, y_end);
  display_set_memory_pointer(x, y);
  display_send_command(WRITE_RAM);

  // ensure that we're sending somthing that's 8bit tall and wide
  // as our display can't handle other resolutions
  if (x_end - x < 8) {
    x_end = x + 8;
  }
  if (y_end - y < 8) {
    y_end = y + 8;
  }

  // send byte by byte
  int data;
  for (int j = 0; j < y_end - y + 1; j++) {
    for (int i = 0; i < (x_end - x + 1) / 8; i++) {
      int index = i + j * (image_width / 8);
      if (stored_on_flash) {
        data = pgm_read_byte(&image_buffer[index]);
      } else if (overwrite > -1) {
        data = overwrite;
      } else {
        data = image_buffer[index];
      }
      display_send_data(invert ? ~data : data);
    }
  }
}
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

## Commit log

2020-11-10 add pitch presentation
2020-12-17 implement spi hardware communication
2020-12-17 fix spi pin numbers
    [spi.c]
2020-12-20 Add I2C & BME280 base
2020-12-20 Add temperature compensation and demo
    Use compensation formula from BME280 datasheet (p.25)
2020-12-21 extra spi pin handling
2020-12-21 WIP: implement display driver
2020-12-27 fix port vs ddr confusion in spi
    [renderer.c, spi.c]
2020-12-27 improved spi commenting
2021-01-04 state machine main program flow draft
2021-01-09 outline program flow in state machine with pseudocode
2021-01-10 Add Fritzing Schematic
    [Fermentation_Box_v1.fzz]
2021-01-18 wip: main program flow
2021-01-18 implement main program flow: fermentation and main menu state switches
2021-01-19 Add basic PWM to PIN 3
2021-01-21 Add Timer set to 1 second
2021-01-22 draft pid controller
2021-01-23 Tune PID to 25°
2021-01-24 Add comment to timer
2021-01-30 Add fast touch. Add auto calibration of touch input
2021-01-31 fix fermentation start flickering
    [main.c]
2021-02-28 Upload fritzing v3
    [Fermentation_Box_v3.fzz]
